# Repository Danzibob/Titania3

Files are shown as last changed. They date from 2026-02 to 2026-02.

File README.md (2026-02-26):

# Titania III
This project is the third iteration of the tiny titania data-logger for model rocketry.

The project goal is to create a datalogger small and light enough for an 18mm A8-3 rocket, but capable enough to use as a backup logger for mid and high power flights.
An additional aim of this project is to run on a rechargable coin cell battery instead of the usual LiPo.
This restriction heavily limits our component choices because of the low current provided by these coin cells (usually <15mA sustained).

## Docs
- [Components List](./hardware/components.md)

## Features
- Logs barometric pressure, temperature, acceleration and rotation data
- Up to 600Hz logging in bursts, 200Hz normal target
- Logs save to flash memory (4MB)
- Buzzer / beeper for basic output & assist in recovery
- PCB-edge USB-A for firmware programming, data offload & charging
- Fits in an 18mm rocket body tube
- Mass of < 10g (including battery)
- LIR1254 rechargable coin cell power source

## Logging format
In order to maximise the logging time available in the flash, we make a trade-off for minimizing storage over precision. This project aims to allow for the following flight timings to fit in the 4MB log flash:

| Flight Phase | Duration (up to) | Storage Priority | Storage Allocation | Max Data Rate |
|---|---|---|---:|---:|
| Pad time | 1 hour | Small constant storage | <1% (~100B) | N/A |
| Ascent | 2 minutes | Most important | ~75% (3 MB) | 25 kB/s |
| Descent | 20 minutes | Less important | ~25% (1 MB) | ~800 B/s |
| Recovery | 2 hours | No storage required | N/A | N/A |

### BMP580
#### Barometric pressure
- Sensor measurement range: 30-125kPa
- Absolute accuracy: +/- 50Pa 
  - Corresponds to ~4m of altitude near sea level
- Relative accuracy: 6Pa per 10kPa
  - ~0.5m / 1km of altitude
  - _Relative accuracy is what's important for determining the altitude of a flight_
- Resolution at oversampling levels (RMS noise @ 100kPa):
  - Low      (1x)   = 0.78Pa @ up to 498Hz
  - Standard (x4)   = 0.41Pa @ up to 255Hz
  - High     (x16)  = 0.21Pa @ up to 87Hz
  - Highest  (x128) = 0.08Pa @ up to 12Hz

On pad, take an f32 Highest resolution sample over a few seconds.
- Massive overkill but nice to have accurate ground pressure

In flight, record u16 pressure with LSB = 2Pa.
- This gives us spatial resolution of ~16cm
- And a range of 0-131kPa, which fully covers the sensor range
- Also easy to convert by bitshifting

#### Temperature
- While ascending, the rocket is moving too fast for the air temperature inside the chassis to equalize
- Therefore, only take temperature readings on the pad and during descent
- Based on the Troposphere lapse rate of ~ 6.5K/km, and the 10km ceiling for this logger, we need to deal with at least a range of 60 degrees
- Combined with a ground temperature range of -10 to 50C this requires a total range of at least 120 degrees
- f16 gives us plenty of resolution within this range

On pad/boot, record a temperature value over several seconds (f16)
- We can combine this with ground pressure for better altitude estimates

Not much point taking temperature readings on ascent
- Could maybe store an i8?

On descent, the barometer will be exposed to the open air at slower speed. 
- Take f16 measurements at regular intervals
- These can be used to accurately profile the air column

#### Sampling & Data Rates
- **Pad** - take a set of samples over a preset startup window (10s?)
  - 6 bytes (f32 pressure and f16 temp)
  - Potentially worth repeating every 30 seconds until launch?
  - Ring buffer to save last N measurements before launch?
- **Ascent** - Log Pressure (and _maybe_ temp) at high frequency
  - 500Hz * u16(+i8) = 1kB/s (1.5kB/s) = 4% (6%) of quota
  - 250Hz * u16(+i8) = 500B/s (750B/s) = 2% (3%) of quota
  - 100Hz * u16(+i8) = 200B/s (300B/s) = <1% (~1%) of quota
- **Descent** - Significantly lower frequency; log pressure & temp at full resolution
  - 10Hz * (u16+f16) = 40B/s = 5% of quota
- **Ground**
  - No logging required

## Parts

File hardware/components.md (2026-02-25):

## Components

### MCU - [STM32L072CBT6](https://www.st.com/resource/en/datasheet/stm32l072v8.pdf)
- Ultra low power
- ARM Cortex M0+ 32kHz - 32MHz
- 128kB internal flash
- 20kB SRAM
- USB Support
  - Pre-programmed bootloader with USB FS
  - No external crystal required

### Barometer - [BMP580](https://www.lcsc.com/datasheet/C22391138.pdf)  <!-- Can't find this on Bosch's website for some reason -->
- Ultra low power
- 30..125kPa
- -40..85C
- up to 622Hz data rate (FORCED or CONTINOUS mode)
  - up to 240Hz in NORMAL mode
- Configurable oversampling & filtering

### IMU - [BMI260](https://www.smart-chips.cn/wp-content/uploads/2025/10/BST-BMI260-DS000-01_typ_final.pdf) <!-- Can't find this on Bosch's website for some reason -->
- Ultra low power (typ 0.7mA)
- 6 axis (acceleration & gyro)
- +/- 16g @ up to 1.6kHz
- +/- 2000dps @ up to 6.4kHz
- Configurable oversampling & filtering

### External Flash - [MX25R3235FM1IL0](https://www.macronix.com/Lists/Datasheet/Attachments/8755/MX25R3235F,%20Wide%20Range,%2032Mb,%20v1.8.pdf)
- Ultra low power (max 6mA bursts on write, typ 3.5mA)
- 4MB storage (32Mbit)
- Accessed via SPI

### Battery Charging - [MCP73831T-2ATI/OT](https://ww1.microchip.com/downloads/en/DeviceDoc/MCP73831-Family-Data-Sheet-DS20001984H.pdf)
- 4.2V CCCV
- 15-500mA configurable (we use the minimum of 15mA)
- Automatic power-down

### Voltage Regulator (LDO) - [XC6206P332MR-G](https://jlcpcb.com/api/file/downloadByFileSystemAccessId/8579707861620228096)
- JLC Basic component
- 3.3V 200mA output
- Will function down to 3.6V battery voltage
  - This gives us access to ~70-90% of the battery capacity (varies based on temperature)

### Battery - [LIR1254/LIR1255](https://eemb.oss-accelerate.aliyuncs.com//uploads/20230322/bf76cf810935c483152a5993efdd3994.pdf)
- Any 12mm rechargable coin cell is compatible
- Retained by an M2 bolt and minimal 3D printed chassis
- 45-75mAh capacity depending on brand & age
- Max output current approx. 1C
- Reccomended output current ~0.3C

### Charging LED (Red) - [KT-0603R](https://jlcpcb.com/api/file/downloadByFileSystemAccessId/8550723991833485312)
- JLC Basic component
- 2.4V 20mA
- Amusingly uses more power than the rest of the datalogger combined lol
  - Is only used as a USB charging indicator

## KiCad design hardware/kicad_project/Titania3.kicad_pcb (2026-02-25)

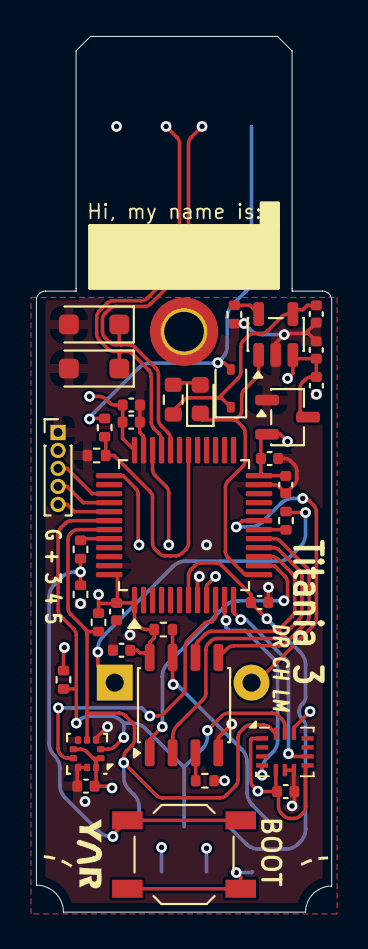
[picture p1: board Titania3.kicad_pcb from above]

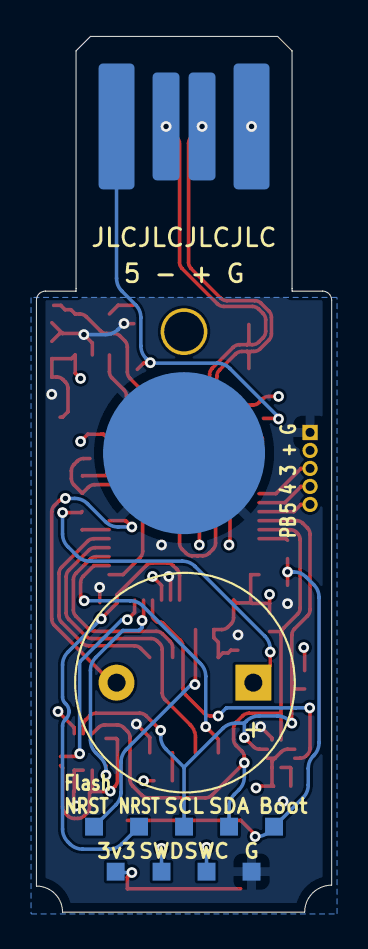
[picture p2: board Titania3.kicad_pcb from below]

Board: 4 copper layers, 16.4 x 48.7 mm, 45 parts (11 on the bottom side), 30 nets.

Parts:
3v3: VDD; TestPoint_Pad_1.0x1.0mm
BZ1: Buzzer; Buzzer_12x9.5RM7.6
Boot: BOOT; TestPoint_Pad_1.0x1.0mm
C1, C2, C12: 4.7uF; C_0402_1005Metric
C3, C4: 1.0uF; C_0402_1005Metric
C5, C6, C7, C8, C9, C11, C13: 100nF; C_0402_1005Metric
D1: LED; LED_0603_1608Metric
D2: 1N5819WS; D_SOD-323
D3: BZT52B3V3; D_SOD-123F
D4: BZT52Bxx; D_SOD-123F
FlashNRST: FLASH_NRST; TestPoint_Pad_1.0x1.0mm
G: VSS; TestPoint_Pad_1.0x1.0mm
J1: USB_A; USB_A_PCB_Edge_receptacle
NRST: NRST; TestPoint_Pad_1.0x1.0mm
R1: 470R (>=250mW); R_0603_1608Metric
R2: 68K; R_0402_1005Metric
R3, R4, R5, R6, R8, R9: 10K; R_0402_1005Metric
R7: 470R; R_0402_1005Metric
R10: 33K; R_0402_1005Metric
R11: 82K; R_0402_1005Metric
SCL: SCL; TestPoint_Pad_1.0x1.0mm
SDA: SDA; TestPoint_Pad_1.0x1.0mm
SW1: BOOT; SW_SPST_TL3342
SWC: SWCLK; TestPoint_Pad_1.0x1.0mm
SWD: SWDIO; TestPoint_Pad_1.0x1.0mm
U1: STM32L072CBT6; LQFP-48_7x7mm_P0.5mm
U2: BMI260; Bosch_LGA-14_3x2.5mm_P0.5mm
U3: BMP580; ST_HLGA-10_2x2mm_P0.5mm_LayoutBorder3x2y
U4: MCP73831; SOT-23-5
U5: MX25R3235FM1IL0; JEITA_SOIC-8_3.9x4.9mm_P1.27mm
U6: XC6206P332MR; SOT-23-3

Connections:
+3V3: 3v3.1, C4.1, C5.1, C6.1, C8.2, C9.2, C11.2, C12.1, C13.1, R3.1, R4.1, R8.2, R9.1, SW1.2, U1.1 (VDD), U1.9 (VDDA), U1.24 (VDD), U1.36 (VDD_USB), U1.48 (VDD), U2.1 (SDO), U2.5 (VDDIO), U2.8 (VDD), U2.12 (CSB), U3.1 (VDDIO), U3.6 (CSB), U3.10 (VDD), U5.8 (VCC), U6.2 (VO)
+BATT: C2.1, C3.1, U4.3 (V_{BAT}), U6.3 (VI)
BMI_INT1: U1.11 (PA1), U2.4 (INT1)
BMI_INT2: U1.12 (PA2), U2.9 (INT2)
BMP_INT: U1.10 (PA0), U3.7 (INT)
CHG_STAT: D1.1 (K), U1.13 (PA3), U4.1 (STAT)
FLASH_CS: U1.14 (PA4), U5.1 (~CS)
FLASH_MISO: U1.16 (PA6), U5.2 (SO/SIO1)
FLASH_MOSI: U1.17 (PA7), U5.5 (SI/SIO0)
FLASH_SCK: U1.15 (PA5), U5.6 (SCLK)
GND: C1.2, C2.2, C3.2, C4.2, C5.2, C6.2, C7.1, C8.1, C9.1, C11.1, C12.2, C13.2, D3.2 (A), D4.2 (A), G.1, J1.4 (GND), R2.1, R5.1, R11.2, U1.8 (VSSA), U1.23 (VSS), U1.35 (VSS), U1.47 (VSS), U2.6 (GNDIO), U2.7 (GND), U3.3 (VSS), U3.5 (SDO), U3.8 (VSS), U3.9 (VSS), U4.2 (V_{SS}), U5.4 (GND), U6.1 (GND)
NRST: C7.2, NRST.1, U1.7 (NRST)
unnamed: BZ1.1 (+), R7.1
unnamed: BZ1.2 (-), U1.19 (PB1)
unnamed: D1.2 (A), R1.2
unnamed: C1.1, D2.1 (K), R1.1, U4.4 (V_{DD})
unnamed: Boot.1, R5.2, R6.2, SW1.1
unnamed: R6.1, U1.44 (BOOT0)
unnamed: R10.2, R11.1, U1.30 (PA9)
unnamed: R7.2, U1.18 (PB0)
unnamed: R2.2, U4.5 (PROG)
unnamed: FlashNRST.1, R9.2, U5.7 (~RESET/SIO3)
unnamed: R8.1, U5.3 (~WP/SIO2)
SCL: R3.2, SCL.1, U1.42 (PB6), U2.13 (SCx), U3.2 (SCK)
SDA: R4.2, SDA.1, U1.43 (PB7), U2.14 (SDx), U3.4 (SDI)
SWCLK: SWC.1, U1.37 (PA14)
SWDIO: SWD.1, U1.34 (PA13)
USB_D+: D4.1 (K), J1.3 (D+), U1.33 (PA12)
USB_D-: D3.1 (K), J1.2 (D-), U1.32 (PA11)
USB_VBUS: D2.2 (A), J1.1 (VBUS), R10.1
